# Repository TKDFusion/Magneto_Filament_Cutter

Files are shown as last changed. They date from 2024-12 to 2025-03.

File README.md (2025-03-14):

# Magneto Filament Cutter

VzBot_Alu_PrintHead_Assembly_2024-Dec-06_06-16-25AM-000_CustomizedView13469795193
#

This Is a Filament cutter I have designed for VzBot Printhead (https://github.com/VzBoT3D/Vz-Printhead-CNC) series and is a direct replacement for the VzBot Adapter Plate adding 2mm to the hotend length. The Magneto Filament Cutter is compatible with Vz-Printhead  with long Goliath (or any other hotend other than Short Goliath).
To be transparent I was heavily inspired by Magnus Hansson and Francois Lamarche's design from the HevORT group. This project would not be possible without the outstanding help and assistance from Mellow3D & BTT/Biqu!

# Compatability
 Printhead/Hotend/Extruder | Verified | Source
 ------------ | ------ | -----
Mellow CNC Aluminium VzBoT 330/235 Printhead | Verified | [AliExpress](https://www.aliexpress.us/item/3256805041195069.html)
Mellow CNC Aluminium RatRig and Hevort Printhead | Verified | [AliExpress](https://www.aliexpress.us/item/3256805552338488.html)
Mellow All Metal CNC ZeroG Printhead | Verified | [AliExpress](https://www.aliexpress.us/item/3256805878890324.html)
Goliath Air / Water V2 | Verified | [AliExpress](https://www.aliexpress.us/item/3256805112047958.html)
Phaetus RAPIDO SERIES | Verified | 
Dragon Hotend | Verified | 
VzHextrudORT LOW PLUS | Verified | [AliExpress](https://www.aliexpress.us/item/3256805934938658.html)
VzHextrudORT LOW | Not Recommended Due to PTFE Not being retained by ECAS/Bowden coupler feeding into HextrudORT as well as no good options for filament guide at the cutter. Review option in STL files and review Read Me for Instructions.| [AliExpress](https://www.aliexpress.us/item/3256804388574096.html)

## Assembly notes.

PTFE 4x1.75-2mm Capricorn or equivalent for heat break 

Hotend | Lengths 
---------|--------
Rapido SERIES | 17 mm 
Dragon UHF | 3 mm
Goliath AIR | 11.5 mm
Goliath Water | 12 mm

Rapido PTFE Placement 17mm

Insert a filament guide before installing the extruder. This guide is necessary for proper cutting action of the filament. This is meant to be a very tight fit into the hextrudort. 

Vz-HextrudORT PLUS

This is a direct replacement for the VzPrinthead Hotend Adapter plate. The original plate utilizes M3x6 screws, this will be changed out for M3x8 screws. When running hotend cooling fan that utilizes the same screws.(Golaith air ducts) willneed to use M3x10s instead of M3x8

Bolt in to Printhead

It is recommended to apply Loctite (linked in [BOM](https://github.com/Treintjes/Magneto_Filament_Cutter/tree/main/BOM)) to these two screws. As you are tightening these two screws bring them to the point of minimizing free play but NOT to the point of adding resistance to motion.

Blue Loctite Application

## Official partners producing this product are

BTT/Biqu 

Mellow3D

BIQU BTT                      Mellow

## If you appreciate what I do please consider supporting me by

[buymeacoffee.com/Trev1AK](https://buymeacoffee.com/trev1ak)

bmc_qr

[Join me on Discord](https://discordapp.com/users/849867873441546250)

## This project is licensed as
License
https://creativecommons.org/licenses/by-nc/4.0

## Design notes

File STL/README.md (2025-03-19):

## Filament guide for Hextrudort Low Plus

Vz-HextrudORT PLUS

Vz-HextrudORT PLUS 2

## Filament Guide For Hextrudort Low

This is holding the printed part guide on the top of the CNC printhead. The file includes options for F3D Racing CNC printheads and Mellow3D CNC printheads. I recommend printing in .15 or smaller layer heights because of the small features of these parts.
Hextrudort Low PTFE Holder

Hextrudort Low PTFE Holder2

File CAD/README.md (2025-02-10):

# VzBot Magneto Filament Cutter

If machining cutter yourself MAKE SURE TO ADJUST MAGNET POCKETS TO YOUR MAGNET SELECTION!

The file is designed for 6x1.5mm magnets due to BTT/MELLOW manufacturing in China. 

Depending on the country you are located in n42sh magnets are available in either metric or SAE and this will change the magnet's dimensions.

N42SH Magnets are required for reliable operational longevity of the cutter, due to the higher operating temps of magnets. 

Magneto Filament Cutter - VzBot Render

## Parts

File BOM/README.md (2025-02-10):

## Bill of Materials
BoxTurtle kits provided by LDO or Isik's Tech come with all of the physical hardware necessary for FilamATrix, but below is the BOM needed to build it.

 Item    | Quantity | Notes | Source
 ----   | -------- | ------ | -----
Blades | 1 | Excel #17A Narrow Chisel Blade is currently the best blade tested but requires narrowing of the blade. Working on a direct-fit blade as well. | [Excel](https://excelblades.com/collections/replacement-blades/products/17a-1-4-narrow-chisel-blade) |
Optional-Blades | 1 | Generic #17 Hobby knife blade, or Generic #4 Hobby knife blade | [Amazon #4](https://a.co/d/7adKvWy) / [Amazon #17](https://a.co/d/gP8vROD)|
N42SH Magnet 6x1.5mm | 2 | High Temp Neodymium Magnets (120c) Non U.S. based. |
Optional-N42SH 1/4"x1/16" | 2 | High Temp Neodymium Magnets (120c) | [KJ Magnets ](https://www.kjmagnetics.com/d41sh-neodymium-high-temp-disc-magnet) |
D3xM2.5x3mm Shoulder Screw | 1 | Loctite Into Place | [AliExpress](https://www.aliexpress.us/item/3256803148945151.html) / [Amazon](https://a.co/d/aiym16b) |
3x6mm .5mm  | 1 | Shim/Washer | [AliExpress](https://www.aliexpress.us/item/3256806418919226.html) / [Amazon](https://a.co/d/gT2xkiK) |
M3x8 Ultra-Low-Profile Socket Head Screw | 3 | Loctite screw that secures Lever to Blade holder. ----     When running Goliath 2510/2010 fan shroud will need 2 M3x10 as well | [AliExpress](https://www.aliexpress.us/item/2251832795659419.html) / [Amazon](https://a.co/d/hkrRllA) |
M3x0.5 x 3 Stainless Grub Screw | 3 | | [AliExpress](https://www.aliexpress.us/item/3256802823276533.html) / [Amazon](https://a.co/d/9oGgG0g) |
Viratite/Loctite | 1 | Vibra-Tite VC-3 Preffered / Secondary Loctite 242 | [Amazon Vibratite](https://a.co/d/2qGUJ2A) / [Amazon Loctite](https://a.co/d/7Vn6hMn)

#
## Assembly Notes

Epoxy magnets into place 

Cut Blades at 17mm length (+/- .5mm)

Do not over-tighten the set screw will crack the blade.

Use drop of Loctite on M3x8 screw that holds Lever to Blade Holder, and on Lever shoulder screw



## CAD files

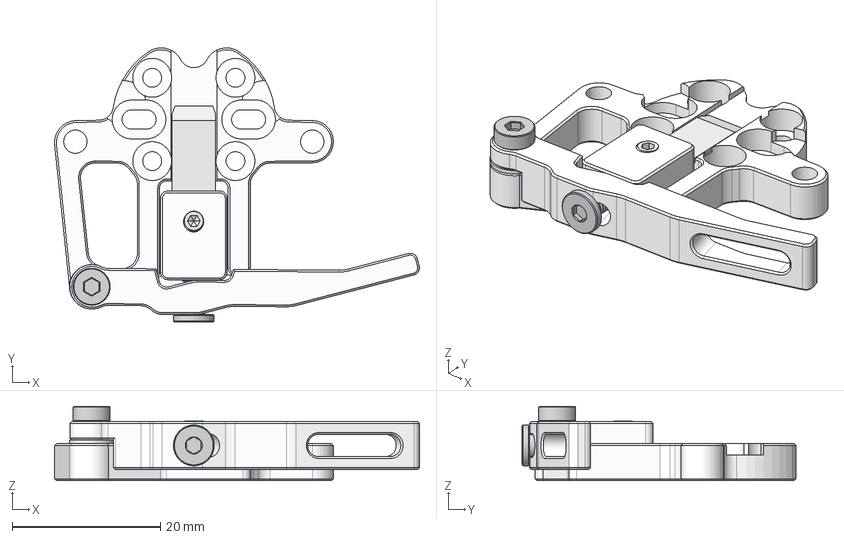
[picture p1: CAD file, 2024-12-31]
CAD/VzBot Magneto Filament Cutter v2 Final.step
49.3 x 37.0 x 10.0 mm
Blade Holder Updated 12/5 to Widened blade holder
Lever Updated 12/5 to fit wider blade holder
.5 Shim 3x6 Stainless Steel
90358A002_Ultra-Low-Profile Socket Head Screw
90265A323_18-8 Stainless Steel Shoulder Screw
N42sh Magnet 6x1.5mm (1)
N42sh Magnet 6x1.5mm (1) (1)
M3x0.5 x 3 Stainless Grub Screw

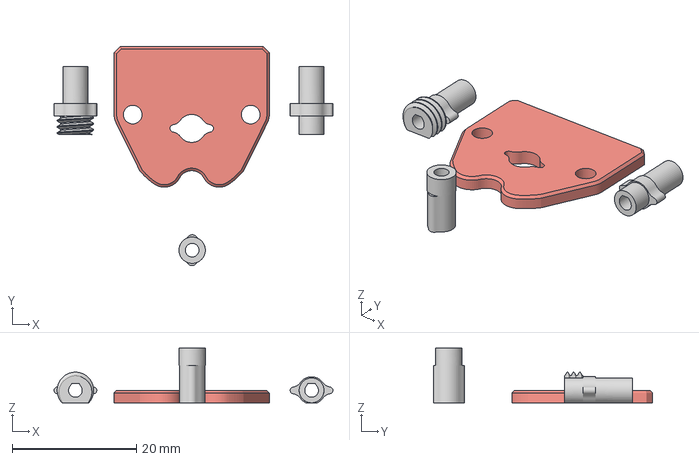
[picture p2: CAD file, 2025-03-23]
STL/Vz-HextrudORT LOW Filament Guide v3.3mf
44.9 x 35.3 x 8.80 mm

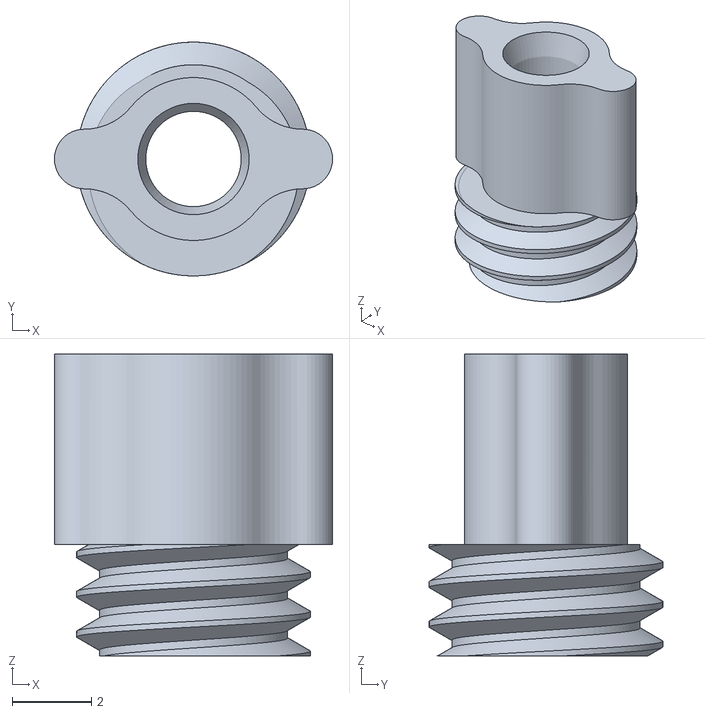
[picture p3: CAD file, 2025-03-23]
STL/Vz-HextrudORT PLUS Filament Guide F3D Racing.stl
7.00 x 5.88 x 7.60

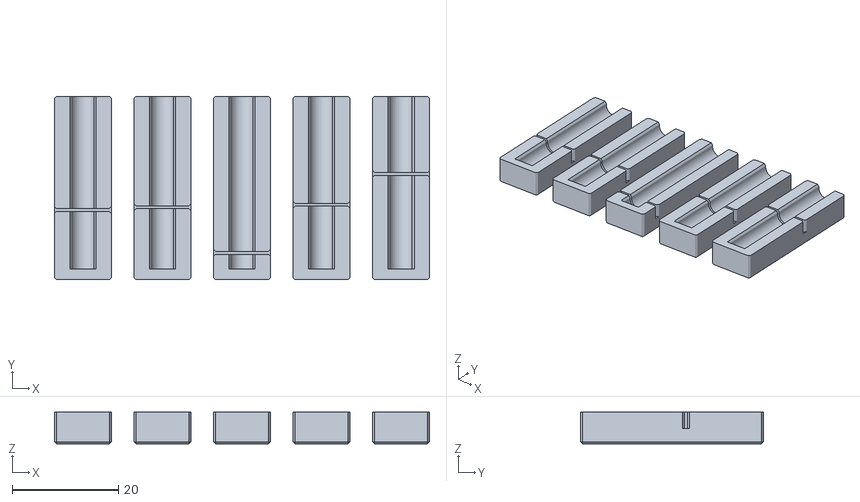
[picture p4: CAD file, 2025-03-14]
STL/PTFE_Cutting_Jigs.stl
70.7 x 34.6 x 6.00

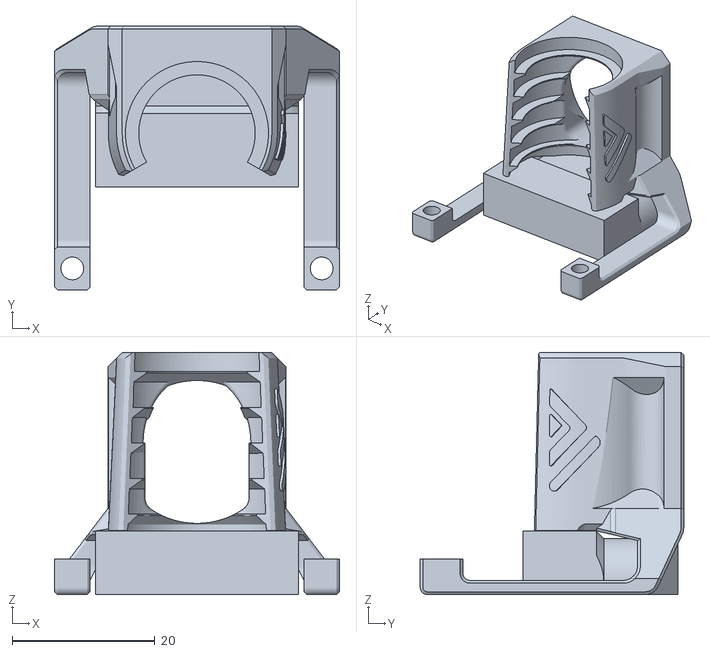
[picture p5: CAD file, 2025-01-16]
STL/Rapido Fan Shroud V2 for Magneto Vz Printhead.stl
40.0 x 37.0 x 34.0

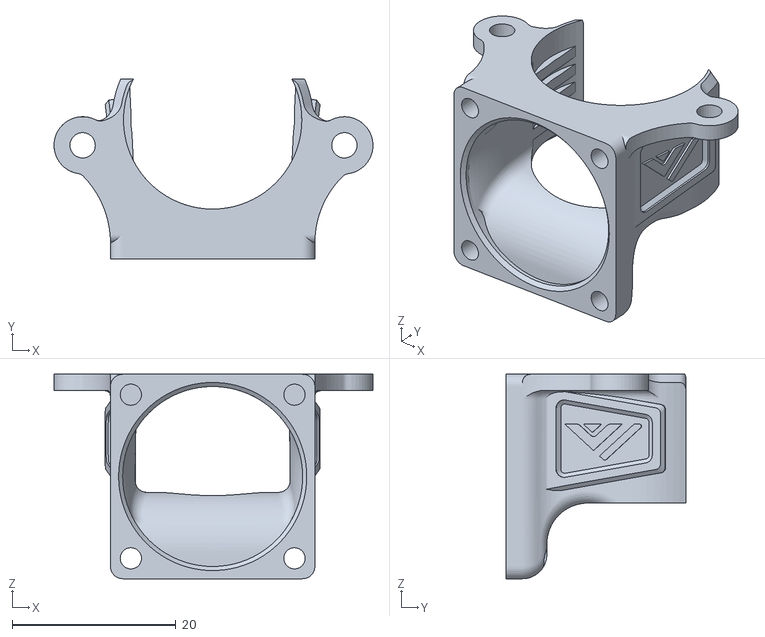
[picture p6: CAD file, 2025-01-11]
STL/Goliath 2510 fan shroud for Magneto Vz Printhead v1.stl
39.0 x 22.0 x 25.0

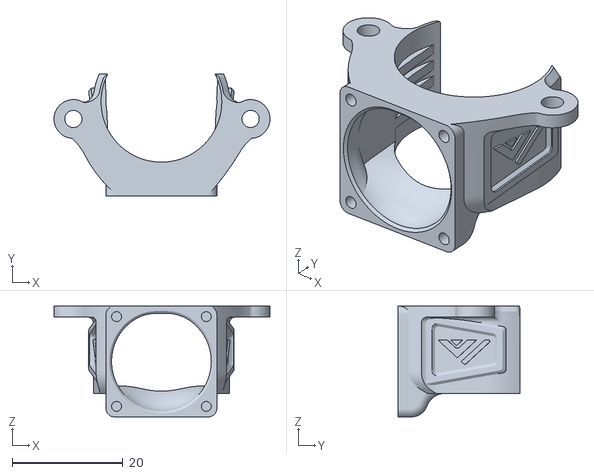
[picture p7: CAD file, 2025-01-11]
STL/Goliath 2010 fan shroud for Magneto Vz Printhead v2.stl
39.0 x 22.0 x 20.0

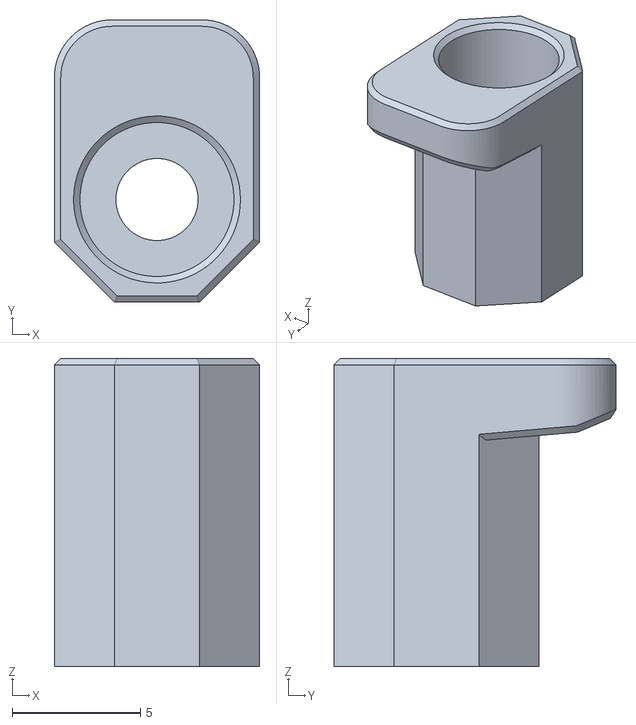
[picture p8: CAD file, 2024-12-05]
STL/Cutter Bump Vz 330 AWD.stl
8.00 x 11.0 x 12.0

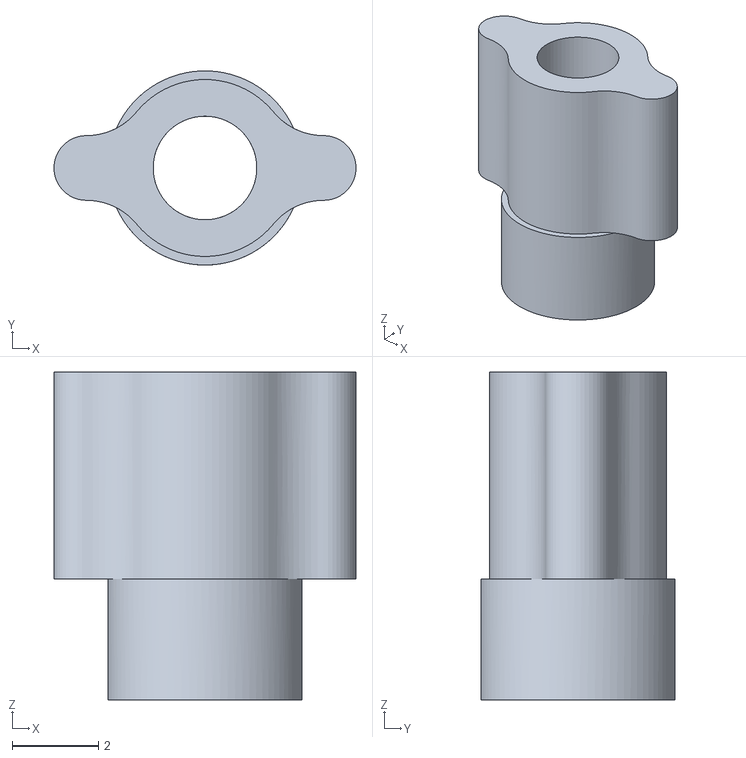
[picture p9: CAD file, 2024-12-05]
STL/Vz-HextrudORT PLUS Filament Guide.stl
7.00 x 4.50 x 7.60

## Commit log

2024-11-10 Create CAD
2024-11-10 Create Magneto Filament Cutter
2024-11-12 Add files via upload
    Updated blade pocket profile
    [Magneto Filament Cutter v2.step]
2024-12-05 Update and rename Filament Cutter VzBot Magneto Updated Blade.step to VzBot Magneto Filament Cutter.step
    [VzBot Magneto Filament Cutter.step]
2024-12-06 v2
    Machining optimizations, and fitted for 6-6.5mm wide blade.
    [VzBot Magneto Filament Cutter v2.step]
2024-12-15 Updated blade profile/holder for manufacturing.
    [VzBot Magneto Filament Cutter v2.step]
2024-12-15 Updated blade profile/holder for manufacturing processes
    [VzBot Magneto Filament Cutter v2.step]
2024-12-16 Updated magnet pockets
    [VzBot Magneto Filament Cutter v2.step]
2024-12-18 Updated to 6mm blade option only.
    [VzBot Magneto Filament Cutter v2.step]
2025-01-11 Create Fan Shrouds
2025-01-16 Add files via upload
    2510 Fan shroud for Rapido on Vz Printhead utilizing Magneto Filament Cutter. This file includes supports in the model.
    [Rapido Fan Shroud V2 for Magneto Vz Printhead.stl]
2025-02-10 Update README.md
    Added Loctite to BOM
2025-02-10 Update README.md
    Added notes regarding magnets
2025-02-10 Add files via upload
    Cutting jigs for hotend PTFE tubes
    [PTFE_Cutting_jigs.stl]
2025-02-10 Update README.md
    reordered assembly
2025-03-10 Rename Cutter Bump Vz 330.stl to Cutter Bump Vz 330 AWD.stl
    [Cutter Bump Vz 330 AWD.stl]
2025-03-14 Add files via upload
    Updated PTFE cutting jigs and added a filament guide for HextrudORT LOW
    [PTFE_cutting_jigs.stl, Vz-HextrudORT LOW Filament Guide.stl]
2025-03-14 Rename PTFE_cutting_jigs.stl to PTFE_Cutting_Jigs.stl
    Updated lengths and added 11mm jig for HextrudORT LOW filament guide
    [PTFE_Cutting_Jigs.stl]
2025-03-19 Add files via upload
    new design for HextrudORT LOW
    [Hextrudort LOW Filament Guide Plate v1.3mf]
2025-03-19 Rename Hextrudort LOW Filament Guide Plate v1.3mf to Vz-HextrudORT LOW Filament Guide Plate v1.3mf
    [Vz-HextrudORT LOW Filament Guide Plate v1.3mf]
2025-03-23 Rename Hextrudort LOW Filament Guide v3.3mf to Vz-HextrudORT LOW Filament Guide v3.3mf
    [Vz-HextrudORT LOW Filament Guide v3.3mf]
